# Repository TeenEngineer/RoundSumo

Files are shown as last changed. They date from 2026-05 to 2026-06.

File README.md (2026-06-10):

# RoundSumo
A sumo robot that I made for km.edu.uz

# Project description
Hello! I made this robot not only for a competition in my local country, Uzbekistan, but I also made it because of statis on hack club. The name for the robot was inspired by the shape of the robot, because it's "round". The code and the CAD files are available. I used 2 SEN0019 IR sensors on the sides, 2 HC-SR04s for the front, 4 line follower sensors for edge detection, and one L298N to power 4 360 RPM motors. I also used an external button for starting the countdown.

# Bill Of Materials:
|Part name |Quantity|Link |
|---|---|---|
|JGA25-370 360 RPM 12V motor|4 |https://ali.click/u0bqd1a|
|HC-SR04 |2 |https://ali.click/vs4zd1c|
|DFRobot SEN0019 |2 |https://ali.click/y4bqd1v|
|ESP-WROOM32 |1 |https://ali.click/bs4zd1g|
|L298N motor driver |1 |https://ali.click/mu4zd1g|
|CR3050B 5V converter |1 |https://ali.click/xebqd1w|
|KY-033 line sensor |4 |https://ali.click/at4zd1n|
|65mm silicone wheel & tire |4 |https://ali.click/rc5zd1hбб(tire), https://ali.click/pd5zd10(wheel and couplings)|

# CAD
Here is a screenshot of what the robot in CAD form looks like:



# Circuit diagram
Also, here is the circuit diagram for my ESP32(Check pinout on your specific model of esp32, because I used esp-wroom32, while you may be using another model. Connect pins according to your diagram):



# Pinouts
And here are the pinouts, just in case:

IR SENSORS:
Left: 34,
Right: 35

Ultrasonic sensors:
TRIG Left: 4,
ECHO Left: 16,
TRIG Right: 5,
ECHO Right: 17

LINE SENSORS:
Front Left: 32,
Front Right: 33,
Back Left: 21,
Back Right: 22

MOTORS:
ENA: 18,
IN1: 14,
IN2: 27,
IN3: 26,
IN4: 25,
ENB: 19

# The robot in action
**The progress, images of the build are at the bottom**

https://github.com/user-attachments/assets/c455ae6e-ef34-4682-b008-044727d600a6

https://github.com/user-attachments/assets/11a2001b-4e5e-49d3-a010-1698324c45ee

https://github.com/user-attachments/assets/0a8def3c-9945-4a7f-9428-d5f1029c288a

# Progress, images of the build
And, here are some photos of the progress))










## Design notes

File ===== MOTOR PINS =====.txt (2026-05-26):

// ===== MOTOR PINS =====
#define IN1 14
#define IN2 27
#define IN3 26
#define IN4 25
#define ENA 18
#define ENB 19

// ===== BUTTON =====
#define BTN 13

// ===== ULTRASONIC =====
#define TRIG1 4
#define ECHO1 16
#define TRIG2 5
#define ECHO2 17

// ===== IR =====
#define IR1 34
#define IR2 35

// ===== LINE =====
#define L1 32
#define L2 33
#define L3 21
#define L4 22

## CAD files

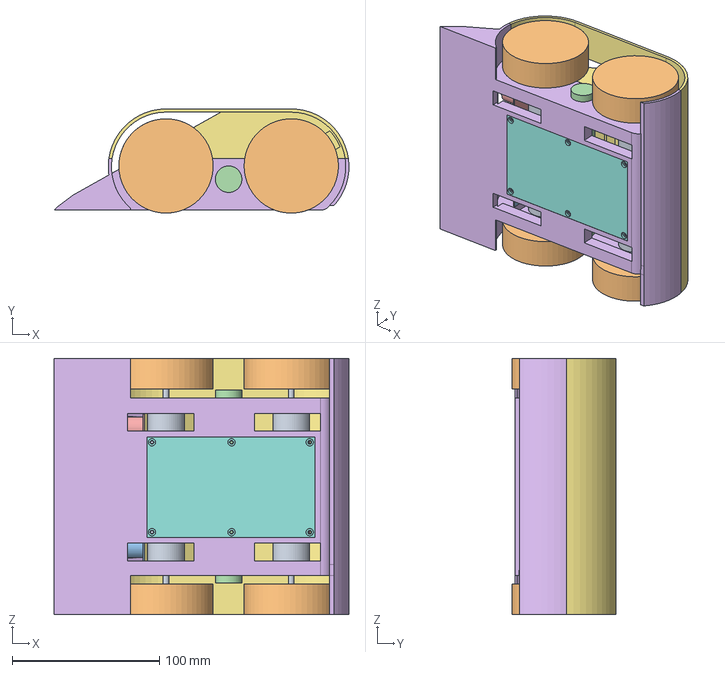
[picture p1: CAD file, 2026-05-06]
RoundSumo.step
200.2 x 70.7 x 174.0 mm

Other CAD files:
Sumo.f3d

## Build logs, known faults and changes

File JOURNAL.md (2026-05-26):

<!--
  This journal is auto generated by Stasis.
-->

# 4/26/2026 11 AM - Coding the new firmware

_Time spent: 1.5h_

Making and testing the improved firmware(still not successful)





Here are some images of the build:
















# 4/25/2026 7 PM - Almost the last step

_Time spent: 3h_

First, I assembled the robot with a new shell, which took almost 2 hours((. I first glued on the sensors with hot glue, then installed the IR sensors, screwed on the motors, and lastly, put super glue in some places so the frame stays strong.














# 4/23/2026 10 AM - 3D printing part 1

_Time spent: 3.75h_

I 3D printed the bottom part of the body along with the lid for it. I designed the enclosure in Fusion360(also raged a little bit), made an electronics assembly consisting of esp32 wroom, 2 SEN0019 sensors, 2 ultrasonic sensors, and 4 line follower sensors. The image provided is the first prototype enclosure.
Screenshot_20260423_132639_Telegram





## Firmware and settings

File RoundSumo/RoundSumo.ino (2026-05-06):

  // ---------- SENSORS ----------
#define IRL 34
#define IRR 35

// ultrasonic sensors:
#define TRIGL 4
#define ECHOL 16
#define TRIGR 5
#define ECHOR 17

// ---------- LINE SENSORS ----------
#define LFL 32
#define LFR 33
#define LBL 21
#define LBR 22
const bool LINE_DETECTED_LOW = false;

// ---------- MOTORS ----------
#define ENA 18
#define IN1 14
#define IN2 27
#define IN3 26
#define IN4 25
#define ENB 19

// ---------- START BUTTON ----------
#define BTN_START 13

// ---------- SPEEDS ----------
const int SPEED_ATTACK = 245;
const int SPEED_TURN = 185;
const int SPEED_CENTER = 190;
const int SPEED_RUSH = 255;
const int SPEED_ESCAPE = 210;
const int SPEED_ESCAPE_BIAS = 150;

// ---------- MOTOR DIRECTION CALIBRATION ----------
// Keep these at 1 if the side moves physically forward for a positive command.
// Set one side to -1 if that side is reversed.
const int LEFT_DRIVE_SIGN = 1;
const int RIGHT_DRIVE_SIGN = 1;

// ---------- ULTRASONIC ----------
const long FRONT_DETECT_CM = 65;
const long FRONT_CLOSE_CM = 35;
const long FRONT_MIN_CM = 2;
const long FRONT_NO_TARGET_CM = 80;
const unsigned long ULTRASONIC_GAP_MS = 20;
const unsigned long FRONT_MEMORY_MS = 200;
const unsigned long IR_MEMORY_MS = 250;
const unsigned long LINE_MEMORY_MS = 120;
const unsigned long FRONT_LOCK_MS = 280;

// ---------- TACTICAL / TIMING ----------
const unsigned long START_DELAY_MS = 5180;
const unsigned long ESCAPE_HOLD_MS = 600;
const unsigned long SEARCH_RESET_MS = 1600;
const unsigned long STARTUP_SETTLE_MS = 120;
const unsigned long SEARCH_KICK_MS = 90;
const int PWM_FREQ_HZ = 20000;
const unsigned long DEBUG_PRINT_MS = 150;
const unsigned long BRAKE_HOLD_MS = 80;

uint8_t searchDir = 0;  // 0 - right, 1 - left
bool searchDirLocked = false;  // true when set by IR/lock; prevents random override
bool robotOn = false;
bool waitingStart = false;
unsigned long startTimer = 0;
unsigned long robotStartedAt = 0;
uint8_t frontLeftHits = 0;
uint8_t frontRightHits = 0;

unsigned long searchStartTime = 0;
uint8_t searchState = 0;  // 0-turn, 1-pause, 2-fast turn back
unsigned long stateStartTime = 0;

unsigned long lastUltrasonicRead = 0;
bool readLeftUltrasonicNext = true;
long frontLeftDistance = FRONT_NO_TARGET_CM;
long frontRightDistance = FRONT_NO_TARGET_CM;
unsigned long lastFrontLeftSeen = 0;
unsigned long lastFrontRightSeen = 0;
unsigned long lastIrLeftSeen = 0;
unsigned long lastIrRightSeen = 0;
unsigned long lastLineFLSeen = 0;
unsigned long lastLineFRSeen = 0;
unsigned long lastLineBLSeen = 0;
unsigned long lastLineBRSeen = 0;

bool escapeActive = false;
unsigned long escapeUntil = 0;
int escapeLeftSpeed = 0;
int escapeRightSpeed = 0;

unsigned long lastDebugPrint = 0;
bool brakeRushActive = false;
unsigned long brakeRushUntil = 0;
bool frontLockActive = false;
unsigned long frontLockUntil = 0;
int frontLockDirection = 0;  // -1 left, 1 right, 0 centered/unknown

// ---------- MOTOR FUNCTIONS ----------

void motorsStop() {
  analogWrite(ENA, 0);
  analogWrite(ENB, 0);
  digitalWrite(IN1, LOW);
  digitalWrite(IN2, LOW);
  digitalWrite(IN3, LOW);
  digitalWrite(IN4, LOW);
}

void driveRaw(int leftSpeed, int rightSpeed) {
  leftSpeed *= LEFT_DRIVE_SIGN;
  rightSpeed *= RIGHT_DRIVE_SIGN;

  leftSpeed = constrain(leftSpeed, -255, 255);
  rightSpeed = constrain(rightSpeed, -255, 255);

  // Positive = physical forward on this robot.
  digitalWrite(IN1, leftSpeed < 0);
  digitalWrite(IN2, leftSpeed > 0);
  digitalWrite(IN3, rightSpeed < 0);
  digitalWrite(IN4, rightSpeed > 0);

  analogWrite(ENA, abs(leftSpeed));
  analogWrite(ENB, abs(rightSpeed));
}

void motorsForward(int spd) {
  driveRaw(spd, spd);
}

void motorsBackward(int spd) {
  driveRaw(-spd, -spd);
}

void motorsTurnLeft(int spd) {
  driveRaw(-spd, spd);
}

void motorsTurnRight(int spd) {
  driveRaw(spd, -spd);
}

void motorsArcLeft(int leftSpd, int rightSpd) {
  driveRaw(leftSpd, rightSpd);
}

void motorsArcRight(int leftSpd, int rightSpd) {
  driveRaw(leftSpd, rightSpd);
}

// ---------- SENSOR HELPERS ----------

bool isSideEnemyDetected(uint8_t sensorPin) {
  return digitalRead(sensorPin) == LOW;
}

bool isLineDetected(uint8_t sensorPin) {
  int value = digitalRead(sensorPin);
  return LINE_DETECTED_LOW ? (value == LOW) : (value == HIGH);
}

long readUltrasonicCm(uint8_t trigPin, uint8_t echoPin) {
  digitalWrite(trigPin, LOW);
  delayMicroseconds(2);
  digitalWrite(trigPin, HIGH);
  delayMicroseconds(10);
  digitalWrite(trigPin, LOW);

  unsigned long duration = pulseIn(echoPin, HIGH, 10000);
  if (duration == 0) {
    return FRONT_NO_TARGET_CM;
  }

  long distance = (long)(duration * 0.0343f / 2.0f);
  if (distance <= 0 || distance > FRONT_NO_TARGET_CM) {
    return FRONT_NO_TARGET_CM;
  }

  return distance;
}

void updateFrontSensors() {
  if (millis() - lastUltrasonicRead < ULTRASONIC_GAP_MS) {
    return;
  }

  lastUltrasonicRead = millis();

  // Suppress reads during the first few ms after start so the very first
  // ultrasonic ping (which often returns junk) cannot phantom-lock the robot.
  if (robotStartedAt != 0 && millis() - robotStartedAt < STARTUP_SETTLE_MS) {
    return;
  }

  if (readLeftUltrasonicNext) {
    frontLeftDistance = readUltrasonicCm(TRIGL, ECHOL);
    if (isFrontDistanceDetected(frontLeftDistance)) {
      if (frontLeftHits < 2) frontLeftHits++;
      if (frontLeftHits >= 2) {
        lastFrontLeftSeen = millis();
        frontLockActive = true;
        frontLockUntil = millis() + FRONT_LOCK_MS;
        frontLockDirection = -1;
      }
    } else {
      frontLeftHits = 0;
    }
  } else {
    frontRightDistance = readUltrasonicCm(TRIGR, ECHOR);
    if (isFrontDistanceDetected(frontRightDistance)) {
      if (frontRightHits < 2) frontRightHits++;
      if (frontRightHits >= 2) {
        lastFrontRightSeen = millis();
        frontLockActive = true;
        frontLockUntil = millis() + FRONT_LOCK_MS;
        frontLockDirection = 1;
      }
    } else {
      frontRightHits = 0;
    }
  }

  readLeftUltrasonicNext = !readLeftUltrasonicNext;
}

void updateFrontLockState(bool oppFL, bool oppFR) {
  if (oppFL && oppFR) {
    frontLockActive = true;
    frontLockUntil = millis() + FRONT_LOCK_MS;
    frontLockDirection = 0;
    return;
  }

  // Hysteresis: when only one side is currently visible but the lock
  // was already centered, don't snap to that side immediately — only
  // commit to a side after the centered memory has fully decayed.
  if (oppFL) {
    frontLockActive = true;
    frontLockUntil = millis() + FRONT_LOCK_MS;
    if (frontLockDirection != 0) {
      frontLockDirection = -1;
    }
    return;
  }

  if (oppFR) {
    frontLockActive = true;
    frontLockUntil = millis() + FRONT_LOCK_MS;
    if (frontLockDirection != 0) {
      frontLockDirection = 1;
    }
    return;
  }

  if (frontLockActive && millis() >= frontLockUntil) {
    frontLockActive = false;
    frontLockDirection = 0;
  }
}

bool isFrontLeftDetected() {
  return lastFrontLeftSeen != 0 && (millis() - lastFrontLeftSeen) <= FRONT_MEMORY_MS;
}

bool isFrontRightDetected() {
  return lastFrontRightSeen != 0 && (millis() - lastFrontRightSeen) <= FRONT_MEMORY_MS;
}

bool isEnemyCentered() {
  return isFrontLeftDetected() && isFrontRightDetected();
}

bool isFrontDistanceDetected(long distanceCm) {
  return distanceCm >= FRONT_MIN_CM && distanceCm <= FRONT_DETECT_CM;
}

bool isIrLeftDetected() {
  return lastIrLeftSeen != 0 && (millis() - lastIrLeftSeen) <= IR_MEMORY_MS;
}

bool isIrRightDetected() {
  return lastIrRightSeen != 0 && (millis() - lastIrRightSeen) <= IR_MEMORY_MS;
}

bool isLineFLDetected() {
  return lastLineFLSeen != 0 && (millis() - lastLineFLSeen) <= LINE_MEMORY_MS;
}

bool isLineFRDetected() {
  return lastLineFRSeen != 0 && (millis() - lastLineFRSeen) <= LINE_MEMORY_MS;
}

bool isLineBLDetected() {
  return lastLineBLSeen != 0 && (millis() - lastLineBLSeen) <= LINE_MEMORY_MS;
}

bool isLineBRDetected() {
  return lastLineBRSeen != 0 && (millis() - lastLineBRSeen) <= LINE_MEMORY_MS;
}

void motorsHardBrake() {
  digitalWrite(IN1, HIGH);
  digitalWrite(IN2, HIGH);
  digitalWrite(IN3, HIGH);
  digitalWrite(IN4, HIGH);
  analogWrite(ENA, 255);
  analogWrite(ENB, 255);
}

// ---------- EDGE ESCAPE ----------

void startEscape(int leftSpeed, int rightSpeed) {
  escapeActive = true;
  escapeUntil = millis() + ESCAPE_HOLD_MS;
  escapeLeftSpeed = leftSpeed;
  escapeRightSpeed = rightSpeed;
  brakeRushActive = false;
}

bool handleEscape() {
  if (!escapeActive) {
    return false;
  }

  if (millis() >= escapeUntil) {
    escapeActive = false;
    return false;
  }

  driveRaw(escapeLeftSpeed, escapeRightSpeed);
  return true;
}

void startBrakeRush() {
  brakeRushActive = true;
  brakeRushUntil = millis() + BRAKE_HOLD_MS;
}

bool handleBrakeRush() {
  if (!brakeRushActive) {
    return false;
  }

  if (millis() < brakeRushUntil) {
    motorsHardBrake();
    return true;
  }

  brakeRushActive = false;
  motorsForward(SPEED_RUSH);
  return true;
}

void handleLineEscape(bool lineFL, bool lineFR, bool lineBL, bool lineBR) {
  // Allow re-trigger if a new line is detected on the OPPOSITE side
  // of the current escape direction (so we don't drive off the far edge).
  if (escapeActive) {
    bool escapingBackward = escapeLeftSpeed < 0 || escapeRightSpeed < 0;
    bool escapingForward = escapeLeftSpeed > 0 && escapeRightSpeed > 0;
    bool oppositeHit = (escapingBackward && (lineBL || lineBR)) ||
                       (escapingForward && (lineFL || lineFR));
    if (!oppositeHit) {
      return;
    }
  }

  if (lineFL || lineFR) {
    if (lineFL && lineFR) {
      startEscape(-SPEED_ESCAPE, -SPEED_ESCAPE);
    } else if (lineFL) {
      startEscape(-SPEED_ESCAPE, -SPEED_ESCAPE_BIAS);
    } else {
      startEscape(-SPEED_ESCAPE_BIAS, -SPEED_ESCAPE);
    }
    return;
  }

  if (lineBL || lineBR) {
    if (lineBL && lineBR) {
      startEscape(SPEED_ESCAPE, SPEED_ESCAPE);
    } else if (lineBL) {
      startEscape(SPEED_ESCAPE, SPEED_ESCAPE_BIAS);
    } else {
      startEscape(SPEED_ESCAPE_BIAS, SPEED_ESCAPE);
    }
  }
}

// ---------- SEARCH ----------

void resetSearchState() {
  searchStartTime = 0;
  searchDirLocked = false;
}

void aggressiveSearchInPlace() {
  unsigned long now = millis();

  if (searchStartTime == 0) {
    searchStartTime = now;
    if (!searchDirLocked) {
      searchDir = random(0, 2);
    }
  }

  // Kick: during the first SEARCH_KICK_MS of a fresh spin, drive the
  // outer side beyond steady-state with the inner side actively braked.
  // This breaks static friction faster than a pure pivot.
  bool kicking = (now - searchStartTime) < SEARCH_KICK_MS;

  if (searchDir == 0) {
    if (kicking) {
      // Right pivot kick: outer (left) full forward, inner (right) full reverse + brake
      driveRaw(255, -255);
    } else {
      motorsTurnRight(255);
    }
  } else {
    if (kicking) {
      driveRaw(-255, 255);
    } else {
      motorsTurnLeft(255);
    }
  }

  if (now - searchStartTime > SEARCH_RESET_MS) {
    searchStartTime = now;
    if (!searchDirLocked) {
      searchDir = !searchDir;
    }
  }
}

// ---------- ATTACK ----------

void smartAttack(bool oppL, bool oppFL, bool oppFR, bool oppR) {
  // oppFL / oppFR are now memory-based, so they stay stable across the
  // alternating ultrasonic read pattern. Use them directly to avoid
  // single-frame flapping into the wrong branch.
  bool oppFC = oppFL && oppFR;

  if (oppFC) {
    bool veryClose =
      (frontLeftDistance >= FRONT_MIN_CM && frontLeftDistance <= FRONT_CLOSE_CM) ||
      (frontRightDistance >= FRONT_MIN_CM && frontRightDistance <= FRONT_CLOSE_CM);
    motorsForward(veryClose ? SPEED_RUSH : SPEED_ATTACK);
    return;
  }

  // Only ONE ultrasonic sees the target — pivot HARD toward that side
  // until both ultrasonics confirm before we charge.
  if (oppFL) {
    searchDir = 1;
    searchDirLocked = true;
    motorsTurnLeft(255);
    return;
  }

  if (oppFR) {
    searchDir = 0;
    searchDirLocked = true;
    motorsTurnRight(255);
    return;
  }

  // IR-only detection: spin toward the side that sees the enemy NOW.
  // This must come before the frontLock fall-through so the side IRs
  // can override a stale "centered" lock.
  if (oppL && !oppR) {
    searchDir = 1;
    searchDirLocked = true;
    motorsTurnLeft(255);
    return;
  }
  if (oppR && !oppL) {
    searchDir = 0;
    searchDirLocked = true;
    motorsTurnRight(255);
    return;
  }

  if (frontLockActive) {
    if (frontLockDirection < 0) {
      searchDir = 1;
      searchDirLocked = true;
      motorsTurnLeft(255);
      return;
    }
    if (frontLockDirection > 0) {
      searchDir = 0;
      searchDirLocked = true;
      motorsTurnRight(255);
      return;
    }
    // Centered lock with no current detection on either side.
    // Inch forward only briefly; then fall through to search.
    if (oppL && oppR) {
      motorsForward(SPEED_ATTACK);
      return;
    }
    // No corroborating sensor: don't drive blind, search instead.
  }

  aggressiveSearchInPlace();
}

// ---------- START BUTTON ----------

void handleStartButton() {
  static bool lastState = HIGH;
  bool state = digitalRead(BTN_START);

  if (lastState == HIGH && state == LOW) {
    delay(30);
    if (digitalRead(BTN_START) == LOW) {
      if (!robotOn && !waitingStart) {
        waitingStart = true;
        startTimer = millis();
        searchDir = random(0, 2);
      } else if (robotOn) {
        robotOn = false;
        waitingStart = false;
        motorsStop();
        escapeActive = false;
        frontLockActive = false;
        frontLockDirection = 0;
      }
    }
  }

  lastState = state;

  if (waitingStart && millis() - startTimer >= START_DELAY_MS) {
    waitingStart = false;
    robotOn = true;
    resetSearchState();
    frontLockActive = false;
    frontLockDirection = 0;
    frontLeftHits = 0;
    frontRightHits = 0;
    frontLeftDistance = FRONT_NO_TARGET_CM;
    frontRightDistance = FRONT_NO_TARGET_CM;
    lastFrontLeftSeen = 0;
    lastFrontRightSeen = 0;
    lastIrLeftSeen = 0;
    lastIrRightSeen = 0;
    lastLineFLSeen = 0;
    lastLineFRSeen = 0;
    lastLineBLSeen = 0;
    lastLineBRSeen = 0;
    robotStartedAt = millis();
    // searchDir already randomized at button press; keep it.
    searchDirLocked = false;
  }
}

// ---------- DEBUG ----------

void printDebug(bool lineFL, bool lineFR, bool lineBL, bool lineBR, bool oppL, bool oppFL, bool oppFR, bool oppR) {
  if (millis() - lastDebugPrint < DEBUG_PRINT_MS) {
    return;
  }

  lastDebugPrint = millis();

  Serial.print("LFL:");
  Serial.print(digitalRead(LFL));
  Serial.print("(");
  Serial.print(lineFL ? "ON" : "off");
  Serial.print(") LFR:");
  Serial.print(digitalRead(LFR));
  Serial.print("(");
  Serial.print(lineFR ? "ON" : "off");
  Serial.print(") LBL:");
  Serial.print(digitalRead(LBL));
  Serial.print("(");
  Serial.print(lineBL ? "ON" : "off");
  Serial.print(") LBR:");
  Serial.print(digitalRead(LBR));
  Serial.print("(");
  Serial.print(lineBR ? "ON" : "off");
  Serial.print(") | IRL:");
  Serial.print(oppL ? "ON" : "off");
  Serial.print(" IRR:");
  Serial.print(oppR ? "ON" : "off");
  Serial.print(" | USL:");
  Serial.print(frontLeftDistance);
  Serial.print("cm(");
  Serial.print(oppFL ? "ON" : "off");
  Serial.print(") USR:");
  Serial.print(frontRightDistance);
  Serial.print("cm(");
  Serial.print(oppFR ? "ON" : "off");
  Serial.println(")");
}

// ---------- SETUP ----------

void setup() {
  Serial.begin(115200);

  pinMode(IRL, INPUT);
  pinMode(IRR, INPUT);

  pinMode(TRIGL, OUTPUT);
  pinMode(ECHOL, INPUT);
  pinMode(TRIGR, OUTPUT);
  pinMode(ECHOR, INPUT);

  pinMode(LFL, INPUT_PULLUP);
  pinMode(LFR, INPUT_PULLUP);
  pinMode(LBL, INPUT_PULLUP);
  pinMode(LBR, INPUT_PULLUP);

  pinMode(IN1, OUTPUT);
  pinMode(IN2, OUTPUT);
  pinMode(IN3, OUTPUT);
  pinMode(IN4, OUTPUT);
  pinMode(ENA, OUTPUT);
  pinMode(ENB, OUTPUT);

  // Drive the L298N enable pins at 20kHz instead of the ESP32 default
  // (~1kHz). 1kHz is in the audio band, leaks switching losses, and
  // produces less average torque on a 4-motor / single-driver setup.
  analogWriteFrequency(ENA, PWM_FREQ_HZ);
  analogWriteFrequency(ENB, PWM_FREQ_HZ);

  pinMode(BTN_START, INPUT_PULLUP);

  motorsStop();
  randomSeed(micros());
}

// ---------- MAIN LOOP ----------

void loop() {
  handleStartButton();

  if (!robotOn) {
    motorsStop();
    return;
  }

  bool irLeftNow = isSideEnemyDetected(IRL);
  bool irRightNow = isSideEnemyDetected(IRR);
  bool lineFLNow = isLineDetected(LFL);
  bool lineFRNow = isLineDetected(LFR);
  bool lineBLNow = isLineDetected(LBL);
  bool lineBRNow = isLineDetected(LBR);

  unsigned long now = millis();

  if (irLeftNow) {
    lastIrLeftSeen = now;
    searchDir = 1;
    searchDirLocked = true;
  }

  if (irRightNow) {
    lastIrRightSeen = now;
    searchDir = 0;
    searchDirLocked = true;
  }

  if (lineFLNow) {
    lastLineFLSeen = now;
  }

  if (lineFRNow) {
    lastLineFRSeen = now;
  }

  if (lineBLNow) {
    lastLineBLSeen = now;
  }

  if (lineBRNow) {
    lastLineBRSeen = now;
  }

  // Use memory-based detections to feed the decision logic. This is
  // the main jitter killer: alternating ultrasonic reads + single-frame
  // IR dropouts would otherwise flap detection state every loop.
  bool oppL = isIrLeftDetected();
  bool oppR = isIrRightDetected();
  bool lineFL = isLineFLDetected();
  bool lineFR = isLineFRDetected();
  bool lineBL = isLineBLDetected();
  bool lineBR = isLineBRDetected();

  if (lineFL || lineFR || lineBL || lineBR) {
    handleLineEscape(lineFL, lineFR, lineBL, lineBR);
  }

  if (handleEscape()) {
    printDebug(lineFL, lineFR, lineBL, lineBR, oppL, false, false, oppR);
    return;
  }

  updateFrontSensors();

  bool oppFL = isFrontLeftDetected();
  bool oppFR = isFrontRightDetected();
  updateFrontLockState(oppFL, oppFR);

  printDebug(lineFL, lineFR, lineBL, lineBR, oppL, oppFL, oppFR, oppR);

  if (handleBrakeRush()) {
    return;
  }

  bool anyEnemy = oppL || oppFL || oppFR || oppR;

  if (!anyEnemy && !frontLockActive) {
    aggressiveSearchInPlace();
    return;
  }

  // Transitioning into engagement — reset spin timer once, but DON'T
  // wipe searchDirLocked: IR / front-lock direction must persist.
  if (searchStartTime != 0) {
    searchStartTime = 0;
  }
  smartAttack(oppL, oppFL, oppFR, oppR);
}

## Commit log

2026-04-27 replaced the firmware with the new one
    [RoundSumo.ino]
2026-05-06 added circuit diagram, .step file
    [Circuit Diagram.fzz, RoundSumo.step]
2026-05-06 Update Circuit Diagram.fzz
    [Circuit Diagram.fzz]
2026-05-06 Update README with circuit diagram and pinouts
    Added circuit diagram and pinout details for ESP32.
2026-05-06 Enhance README with CAD screenshot and circuit diagram
    Added a CAD screenshot and updated ESP32 circuit diagram information.
2026-06-03 added BOM
    [BOM.csv]
2026-06-06 Change BOM.csv format from comma to semicolon
    [BOM.csv]
2026-06-06 Fix BOM.csv formatting and remove quotes
    Removed unnecessary quotation marks and adjusted formatting.
    [BOM.csv]
2026-06-06 Fix BOM.csv formatting for proper table rendering
    [BOM.csv]
